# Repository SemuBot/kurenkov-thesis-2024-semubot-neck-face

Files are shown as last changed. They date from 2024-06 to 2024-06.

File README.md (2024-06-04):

# kurenkov-thesis-2024-semubot-neck-face
Author: Nikita Kurenkov

## ENG
This repository contains the table of materials, design files needed for the fabrication and instructions for assembling a neck mechanism for the Social Humanoid Robot SemuBot.






### Materials ###

| Item | Amount | Link to the item |
| ---- | :---: |  ---- |
| 30x30mm Aluminum Spine | 1 | - |
| Nema 11 Stepper L=31mm | 1 | https://www.omc-stepperonline.com/nema-11-stepper-l-31mm-w-rear-shaft-gear-ratio-27-1-planetary-gearbox-11hs12-0674d-pg27 |
| Sliding T Slot Nut M6 for 30x30 extrusion | 3 | - |
| M6 x 6mm Bolt | 3 | - |
| Spine Connector | 1 | https://github.com/incrut/kurenkov-thesis-2024-semubot-neck-face/blob/main/Design/STL/Spine%20Connector.stl |
| M3 x 4mm Phillips Flat Head Bolt | 8 | - |
| M3-0.5 Threaded Heat Set Insert | 20 | - |
| Bearing 65x50x7mm | 1 | - |
| Head Mover | 1 | https://github.com/incrut/kurenkov-thesis-2024-semubot-neck-face/blob/main/Design/STL/Head%20Mover.stl |
| M3 Nut Bolt | 20 | - |
| M3 x 6mm Bolt | 30 | - |
| M3 x 25mm Bolt | 6 | - |
| Bearing Holder - Spine Connector | 1 | https://github.com/incrut/kurenkov-thesis-2024-semubot-neck-face/blob/main/Design/STL/Bearing%20Holder%20-%20Spine%20Connector.stl |
| Head Holder | 1 | https://github.com/incrut/kurenkov-thesis-2024-semubot-neck-face/blob/main/Design/STL/Head%20Holder.stl |
| Snap-Pin Holder | 1 | https://github.com/incrut/kurenkov-thesis-2024-semubot-neck-face/blob/main/Design/STL/Snap-Pin%20Holder.stl |
| Head Holder | 1 | https://github.com/incrut/kurenkov-thesis-2024-semubot-neck-face/blob/main/Design/STL/Head%20Holder.stl |
| 15 x 15 x 20 mm Aluminum Extrusion | 1 | - |
| 15 x 15 x 10 mm Aluminum Extrusion | 1 | - |
| Head Spine Crosser | 1 | https://github.com/incrut/kurenkov-thesis-2024-semubot-neck-face/blob/main/Design/STL/Head%20Spine%20Crosser.stl |
| Mic Mount | 1 | https://github.com/incrut/kurenkov-thesis-2024-semubot-neck-face/blob/main/Design/STL/Mic%20Mount.stl |
| Mic Support | 3 | https://github.com/incrut/kurenkov-thesis-2024-semubot-neck-face/blob/main/Design/STL/Mic%20Support.stl |
| Flexible AMOLED display 7.8 inch | 1 | https://www.alibaba.com/product-detail/7-8-Inch-Flexible-Touch-Screen_1600457566134.html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 |
| Flexible AMOLED display driver | 1 | https://www.alibaba.com/product-detail/7-8-Inch-Flexible-Touch-Screen_1600457566134.html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 |
| M2.5 Nut Bolt | 3 | - |
| M2.5 x 4mm Bolt | 3 | - |
| HDMI to HDMI-mini cable 1m | 1 | - |
| USB-A to USB-C 3.0 cable 1m | 1 | - |

### Items for the Motor Movement Testing ###

| Item | Amount |
| ---- | :---: |
| Arduino Uno | 1 |
| Digital Stepper Driver DM542T | 1 |
| USB-A to USB-B cable | 1 |
| Jumper Wire | 6 |

For Stepper Motor test movement, upload the [script](https://github.com/incrut/kurenkov-thesis-2024-semubot-neck-face/blob/main/Software/stepper_test_movement/stepper_test_movement.ino) to Arduino Uno. When the circuit is assembled, you can control the stepper with keys "w" and "s" to move and "x" to stop movement.
### Circuit Assembly ###
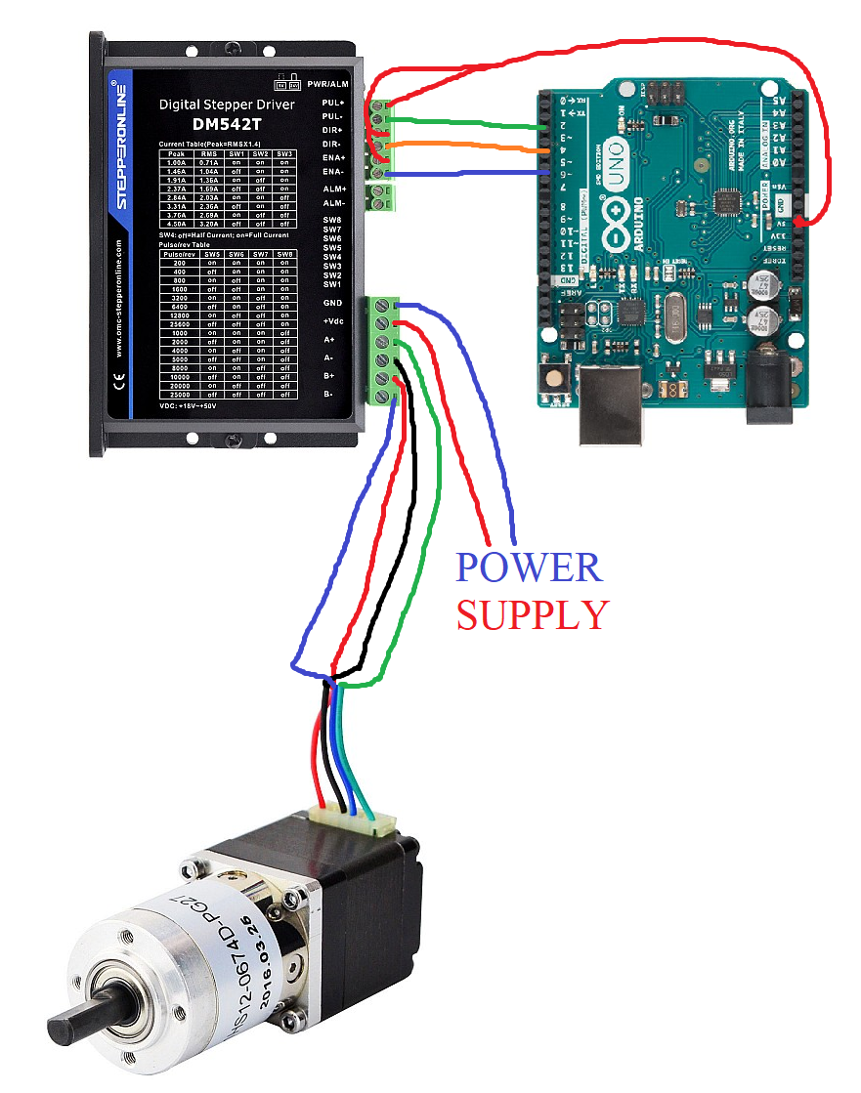
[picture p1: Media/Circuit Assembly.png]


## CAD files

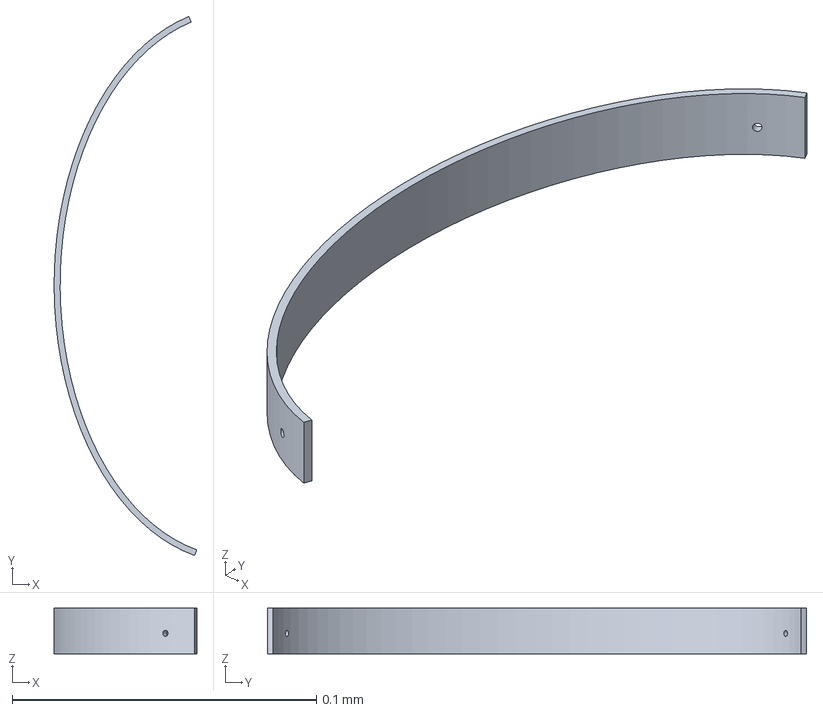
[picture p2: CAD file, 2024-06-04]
Design/3MF/SCREEN HOLDING SUPPORT PLATE.3mf
0.0469 x 0.177 x 0.015 mm

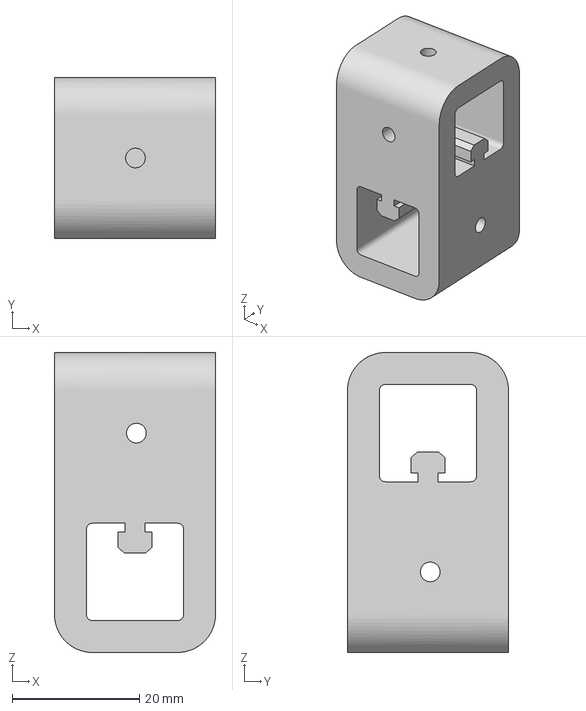
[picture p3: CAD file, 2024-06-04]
Design/3MF/Head Spine Crosser.3mf
25.3 x 25.3 x 47.1 mm

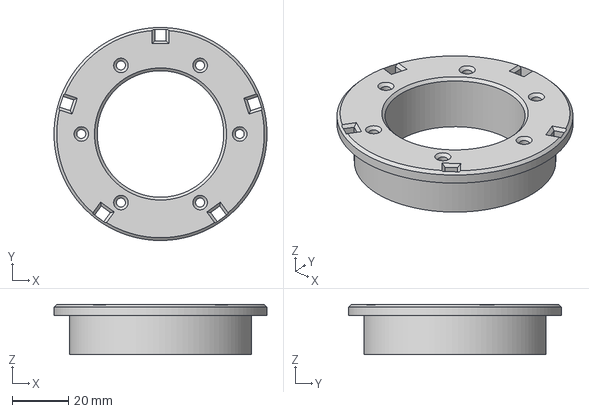
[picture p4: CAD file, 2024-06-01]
Design/3MF/Head connector.3mf
76.0 x 76.0 x 18.0 mm

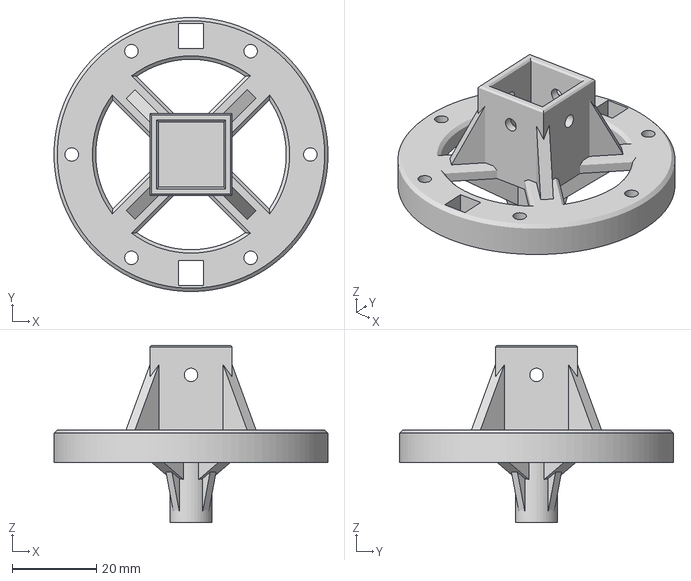
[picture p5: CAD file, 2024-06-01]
Design/3MF/Head mover.3mf
64.9 x 64.9 x 42.0 mm

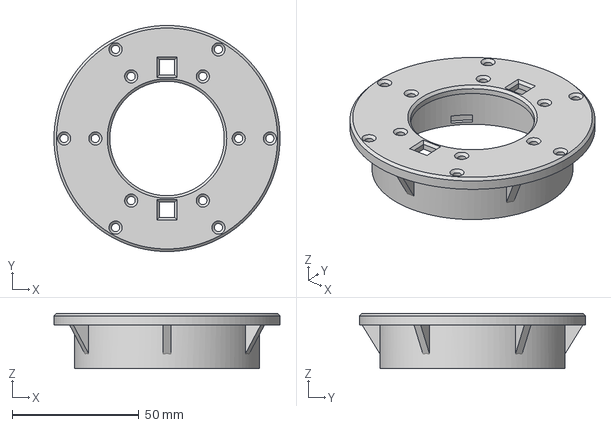
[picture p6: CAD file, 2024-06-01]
Design/3MF/Head Holder.3mf
89.1 x 89.1 x 21.8 mm

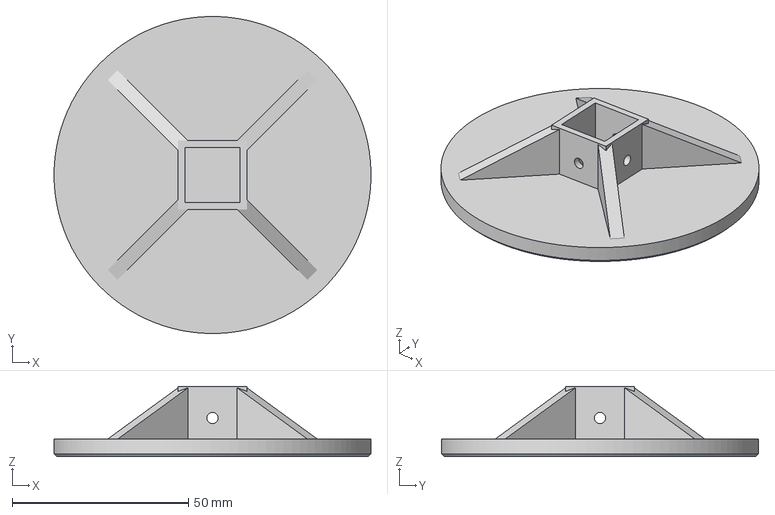
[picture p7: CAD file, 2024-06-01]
Design/3MF/Mic mount.3mf
90.0 x 90.0 x 20.0 mm

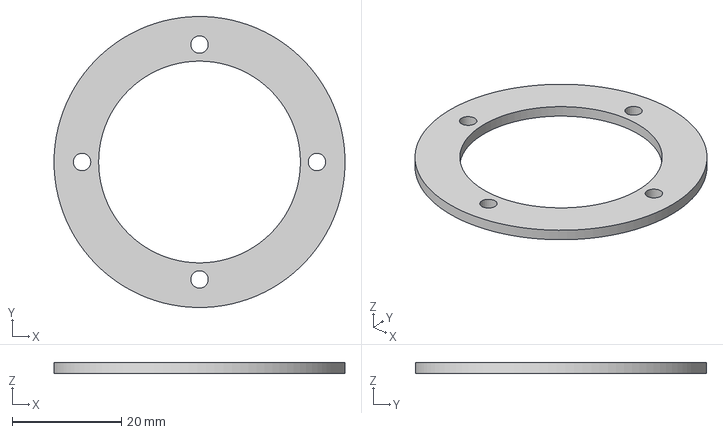
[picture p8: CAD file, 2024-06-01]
Design/3MF/Bearing holder - Spine connector.3mf
53.3 x 53.3 x 2.00 mm

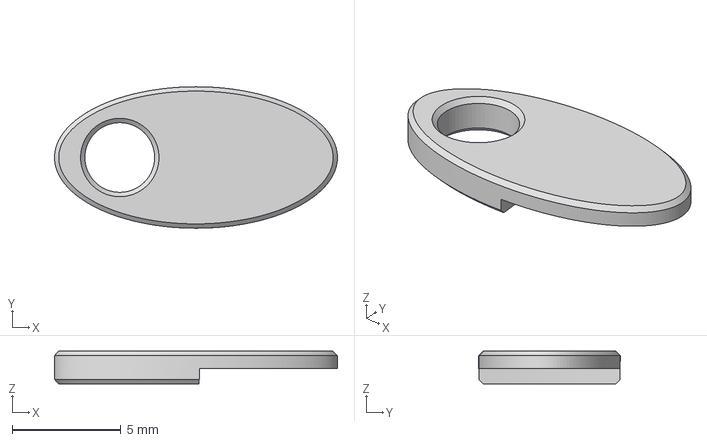
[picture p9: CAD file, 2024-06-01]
Design/3MF/Mic Support.3mf
13.0 x 6.50 x 1.50 mm

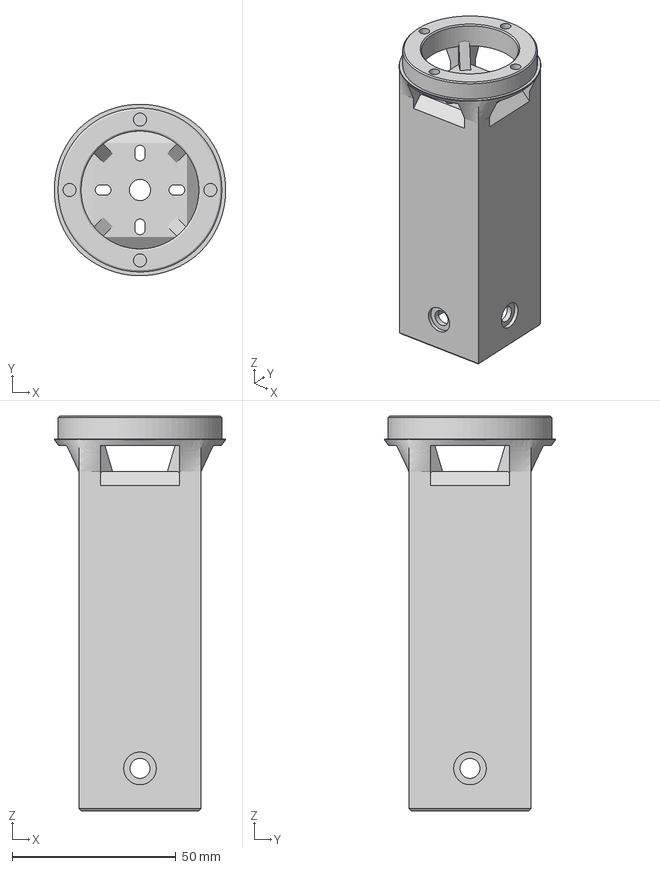
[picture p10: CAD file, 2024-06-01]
Design/3MF/Spine Connector.3mf
52.3 x 52.3 x 120.5 mm

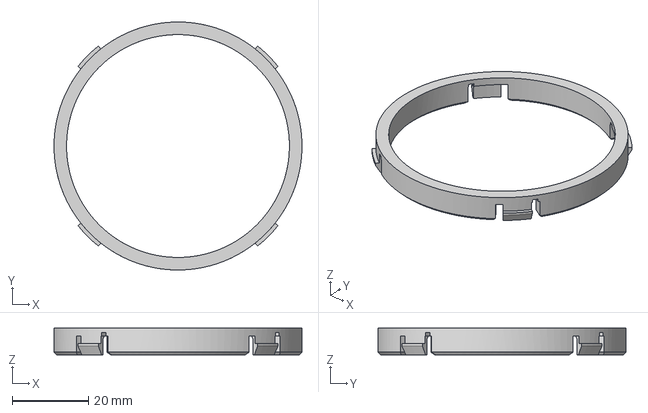
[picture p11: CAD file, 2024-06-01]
Design/3MF/Snap-Pin holder.3mf
65.0 x 65.0 x 7.00 mm

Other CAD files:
Design/STL/Bearing Holder - Spine Connector.stl
Design/STL/Head Connector.stl
Design/STL/Head Holder.stl
Design/STL/Head Mover.stl
Design/STL/Head Spine Crosser.stl
Design/STL/Mic Mount.stl
Design/STL/Mic Support.stl
Design/STL/SCREEN HOLDING SUPPORT PLATE.stl
Design/STL/Snap-Pin Holder.stl
Design/STL/Spine Connector.stl

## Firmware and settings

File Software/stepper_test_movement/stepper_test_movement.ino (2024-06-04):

#include <AccelStepper.h>

#define PUL_PIN 2
#define DIR_PIN 4
#define ENA_PIN 6

// Create an instance of the AccelStepper class
AccelStepper stepper(AccelStepper::DRIVER, PUL_PIN, DIR_PIN);

void setup() {
  // Set the enable pin as output and set it to LOW to enable the driver
  pinMode(ENA_PIN, OUTPUT);
  digitalWrite(ENA_PIN, LOW);

  // Set the maximum speed and acceleration
  stepper.setMaxSpeed(1000); // Adjust the speed as needed
  stepper.setAcceleration(500); // Adjust the acceleration as needed

  // Initialize serial communication
  Serial.begin(9600);
}

void loop() {
  if (Serial.available() > 0) {
    char key = Serial.read();

    if (key == 'w') {
      // Move forward
      stepper.setSpeed(500); // Set a positive speed to move forward
    } 
    else if (key == 's') {
      // Move backward
      stepper.setSpeed(-500); // Set a negative speed to move backward
    } 
    else if (key == 'x') {
      // Stop the motor
      stepper.setSpeed(0); // Set speed to 0 to stop the motor
    }
  }
  // Run the stepper motor
  stepper.runSpeed();
}

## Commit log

2024-06-01 Uploaded STL and 3MF files of the design
    [Bearing Holder - Spine Connector.stl, Bearing holder - Spine connector.3mf, Head Connector.stl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]
2024-06-04 Added Missing Design files and Uploaded some GIFs of the neck assembly
    [Head Spine Crosser.3mf, Head Spine Crosser.stl]
2024-06-04 Uploaded missing model files, Updated README
    [SCREEN HOLDING SUPPORT PLATE.3mf, SCREEN HOLDING SUPPORT PLATE.stl]
2024-06-04 Added a script for stepper test movement
2024-06-04 Added Circuit Assembly picture
